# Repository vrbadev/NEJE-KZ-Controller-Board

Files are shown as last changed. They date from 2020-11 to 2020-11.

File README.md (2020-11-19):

# NEJE-KZ Controller Board
Reverse-engineered schematic and layout for NEJE-KZ laser engraver controller board.

The schematic should be the same as for the original board. Parts should be correctly identified and connected. My goal was to find out the wiring to be able to replace the damaged original board with a board with my own design.

**Warning:** The reconstructed layout has not been manufactured or tested. Weird things can be found on this allegedly $25-worth Chinese board.

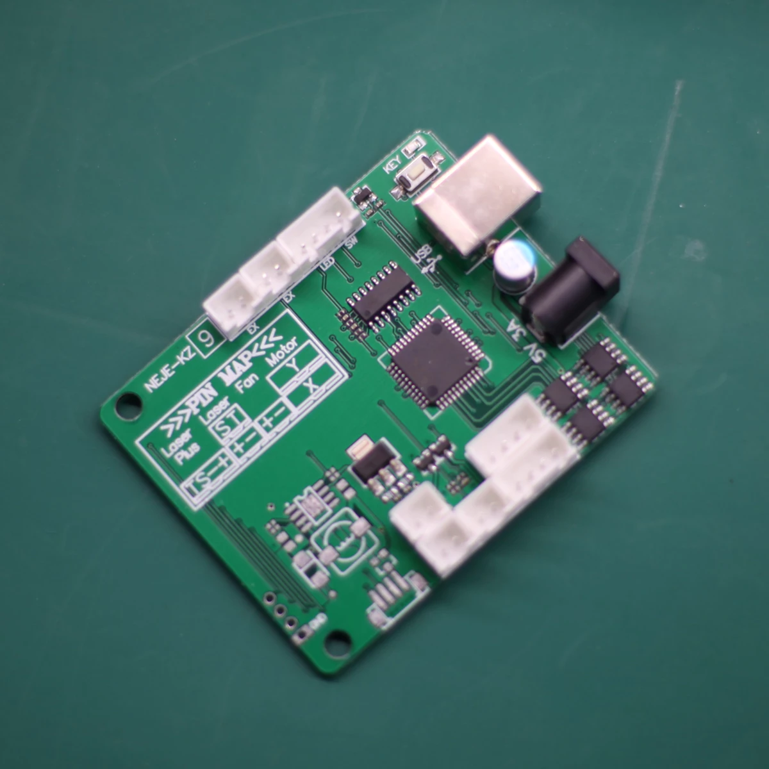
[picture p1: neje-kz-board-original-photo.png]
Original board photo
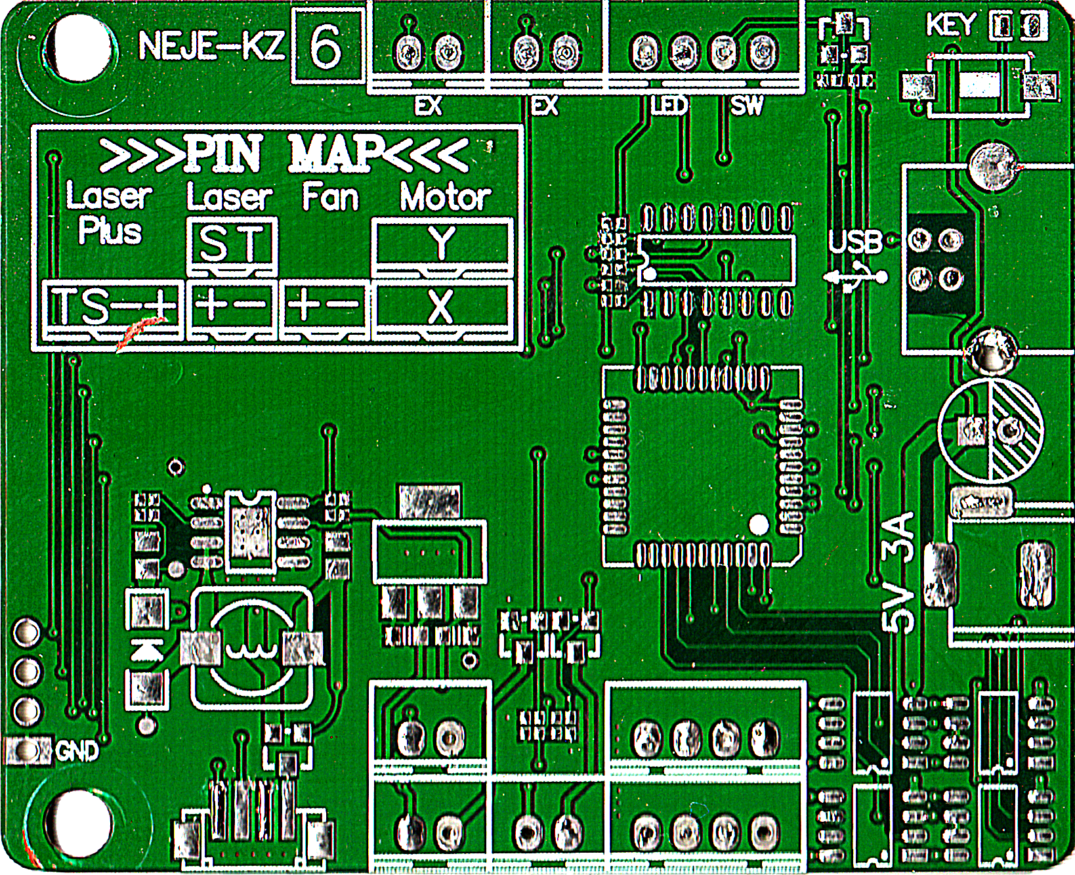
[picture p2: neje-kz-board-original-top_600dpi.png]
Original board - top scan
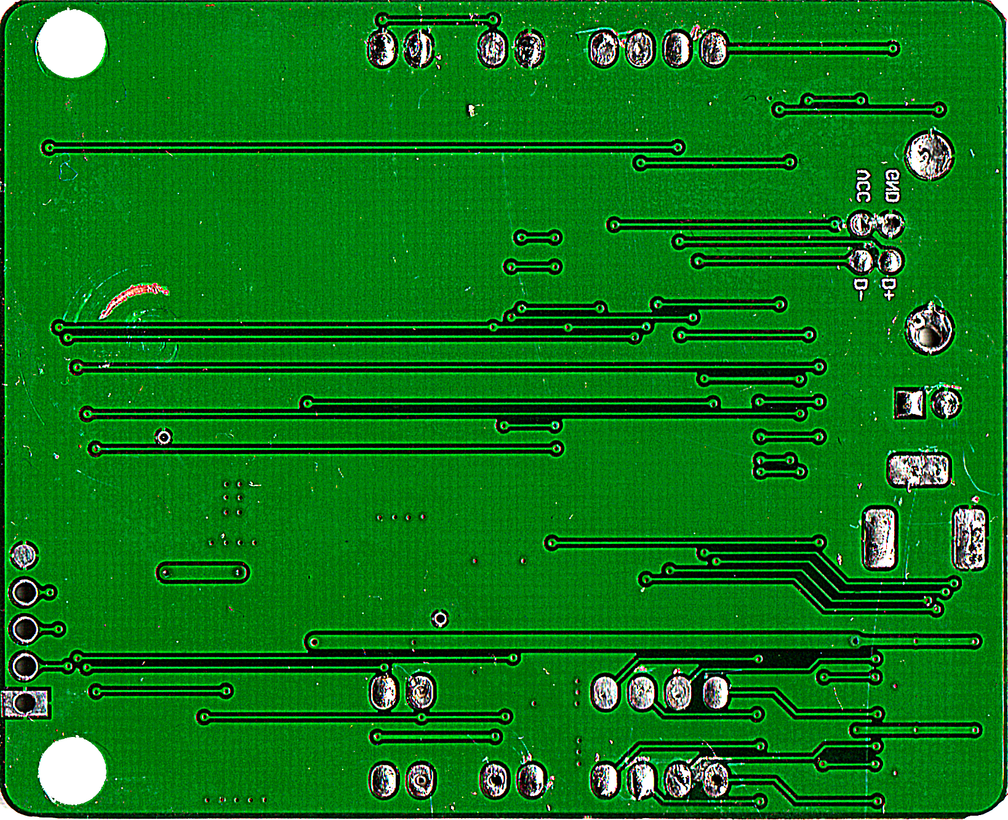
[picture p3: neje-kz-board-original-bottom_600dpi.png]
Original board - bottom scan
  

## BOM
| Qty | Part | Value | Package | Additional info |
|-----|---|---|---|---|
| 1 | C1 | 560u/6.3V | E2,5-7 | |
| 1 | C10 | 1n | 0402 | |
| 4 | C2, C4, C5, C8 | 100n | 0402 | |
| 1 | C3 | 2n7 | 0402 | |
| 2 | C6, C7 | 1u | 0603 | |
| 2 | C9, C11 | 1u | 0805 | |
| 1 | D1 | SS14 | SMA | Schottky diode, 40V, 1A |
| 1 | IC1 | STC8A4K16S2A12 | LQFP44-10X10 | STC8F family MCU |
| 1 | IC2 | XC6206P332MR | SOT23-3 | LDO, 3.3V, 200mA |
| 1 | IC3 | AMS1117-5.0 | SOT223 | LDO, 5.0V, 1A |
| 1 | IC4 | CH340C | SO16 | USB to Serial |
| 1 | IC5 | TX4223 | SOIC8 | DC-DC boost 5A converter |
| 4 | IC6, IC7, IC8, IC9 | TC118S | SOIC8 | Single channel DC motor driver |
| 1 | J1 | USB-B | USB-B-PTH | USB B THT connector |
| 1 | J10 | LASER-ST | JST-XH-02 | |
| 1 | J11 | LASER_PLUS | 1X04_1MM_RA  | |
| 1 | J12 | UART | MA04-1 | |
| 1 | J2 | DC 5.5/2.1mm | | THT DC jack connector |
| 2 | J3, J4 | EX | JST-XH-02 | |
| 1 | J5 | LED-SW | JST-XH-04 | |
| 1 | J6 | MOTOR-X | JST-XH-04 | |
| 1 | J7 | MOTOR-Y | JST-XH-04 | |
| 1 | J8 | FAN | JST-XH-02 | |
| 1 | J9 | LASER-PWR | JST-XH-02 | |
| 1 | L1 | 470UH | 8x8mm | Eg. WE 74477724 |
| 1 | LED1 | | 0805 | |
| 1 | Q1 | SI2301 | SOT23-3 | P-Channel MOSFET |
| 2 | Q2, Q3 | GMS2302AL | SOT23-3 | N-Channel MOSFET |
| 1 | R1 | 1k | 0402 | |
| 5 | R2, R3, R7, R8, R9 | 3k3 | 0402 | |
| 2 | R4, R10 | 10k | 0402 | |
| 1 | R5 | 270R | 0402 | |
| 1 | R6 | 6k2 | 0402 | |
| 1 | S1 | BTN | DTSM-3 | SMT Push-button |

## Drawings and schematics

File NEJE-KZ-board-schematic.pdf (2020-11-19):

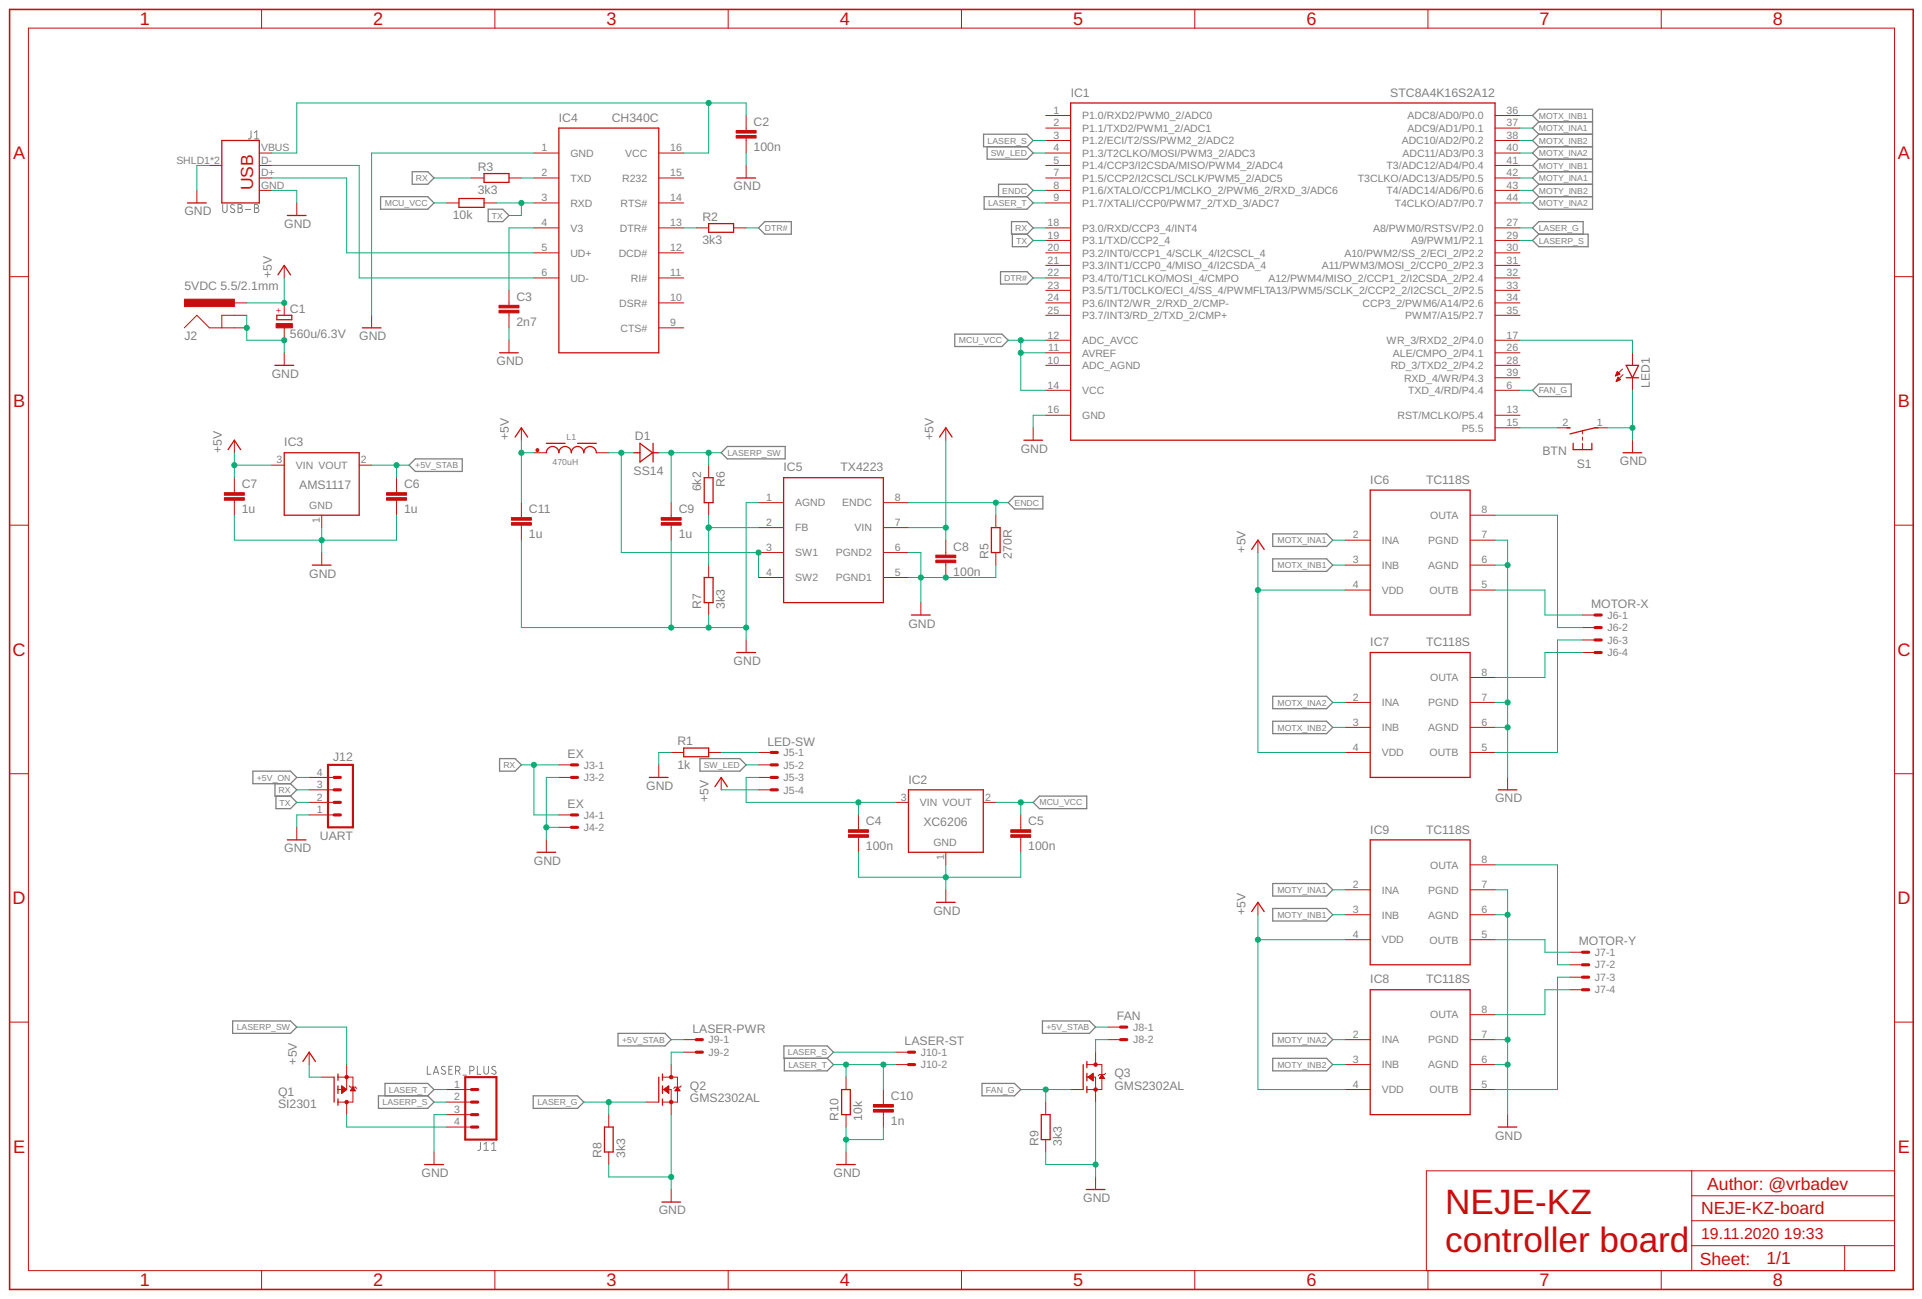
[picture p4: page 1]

TX | LASERP_S

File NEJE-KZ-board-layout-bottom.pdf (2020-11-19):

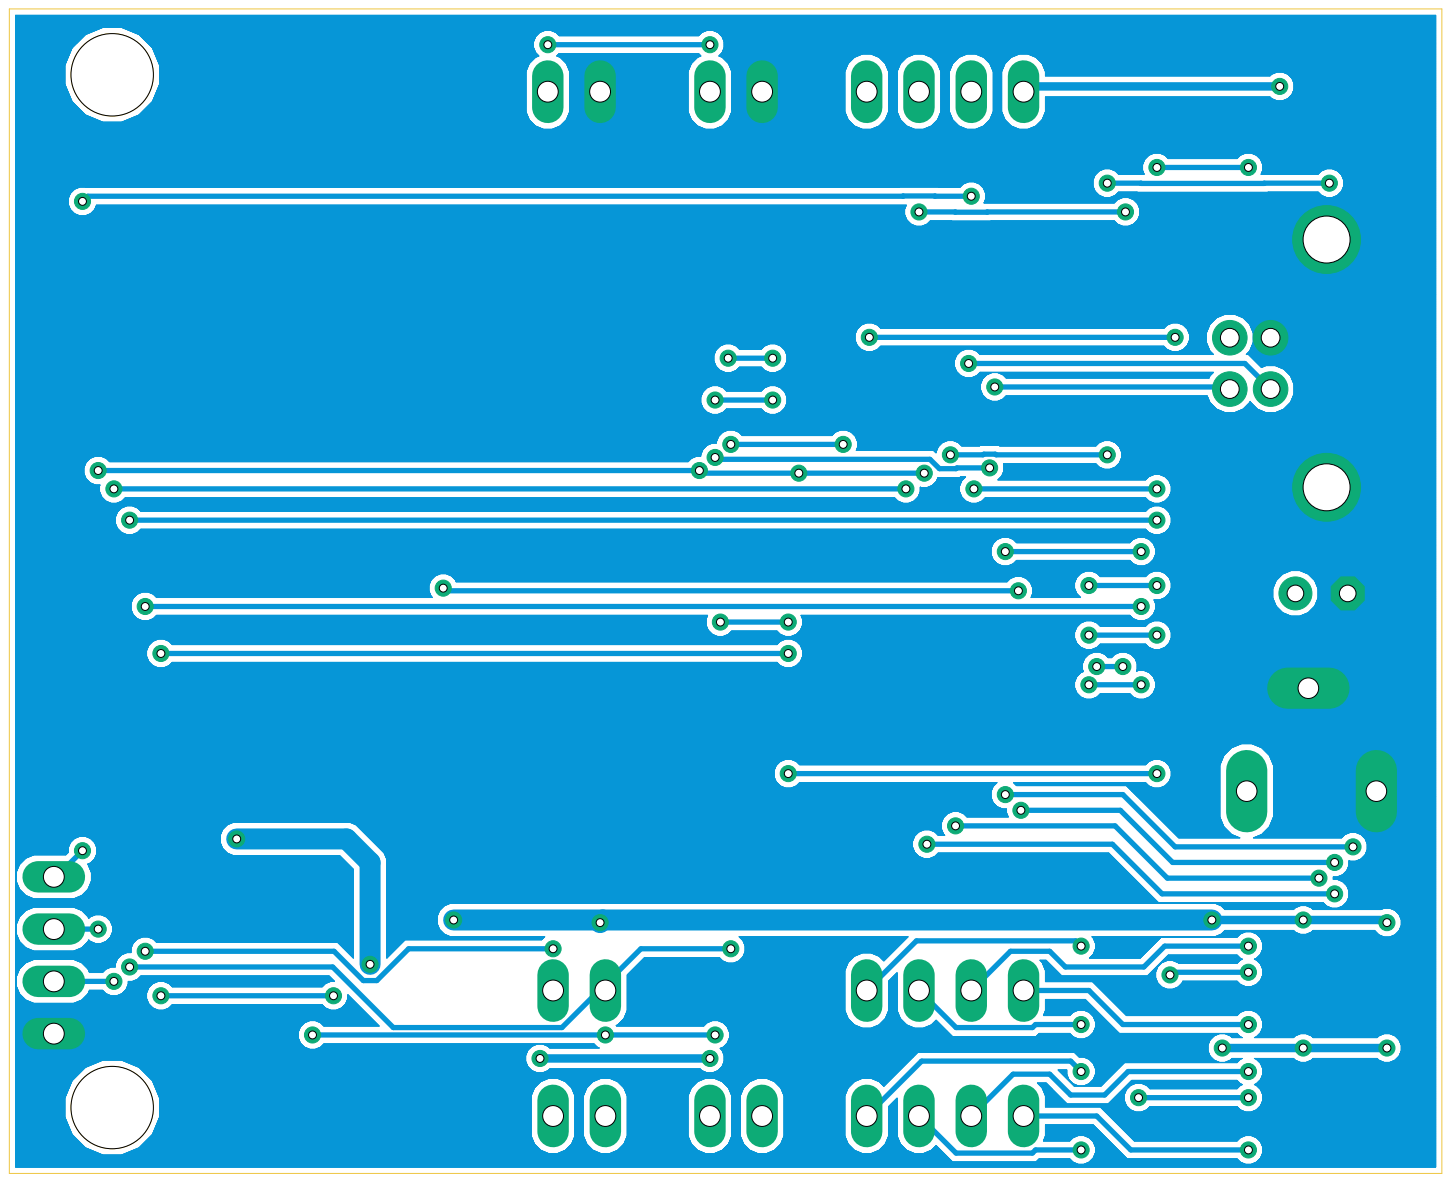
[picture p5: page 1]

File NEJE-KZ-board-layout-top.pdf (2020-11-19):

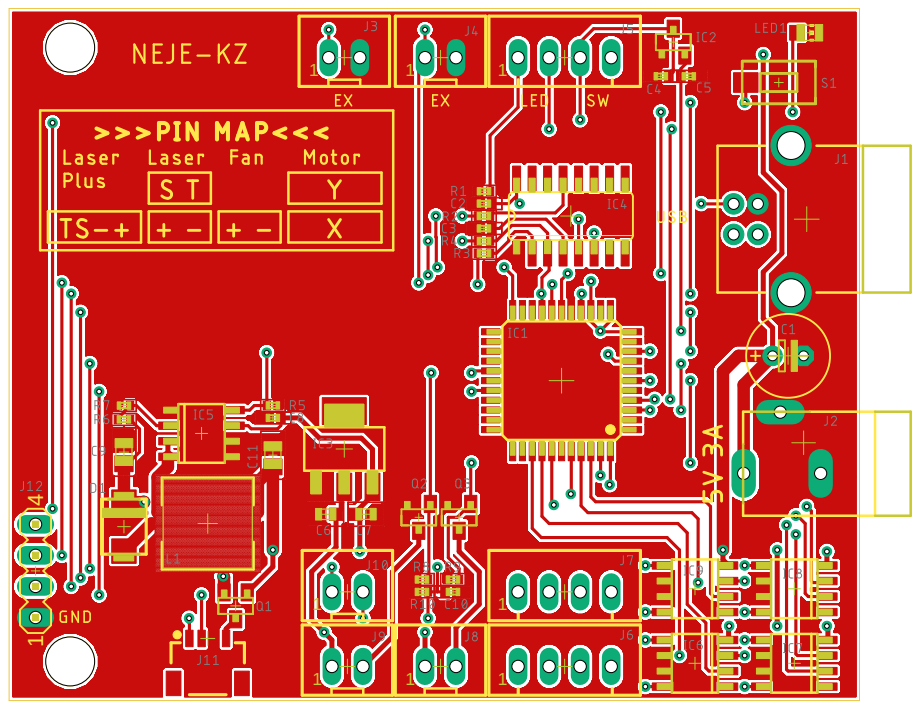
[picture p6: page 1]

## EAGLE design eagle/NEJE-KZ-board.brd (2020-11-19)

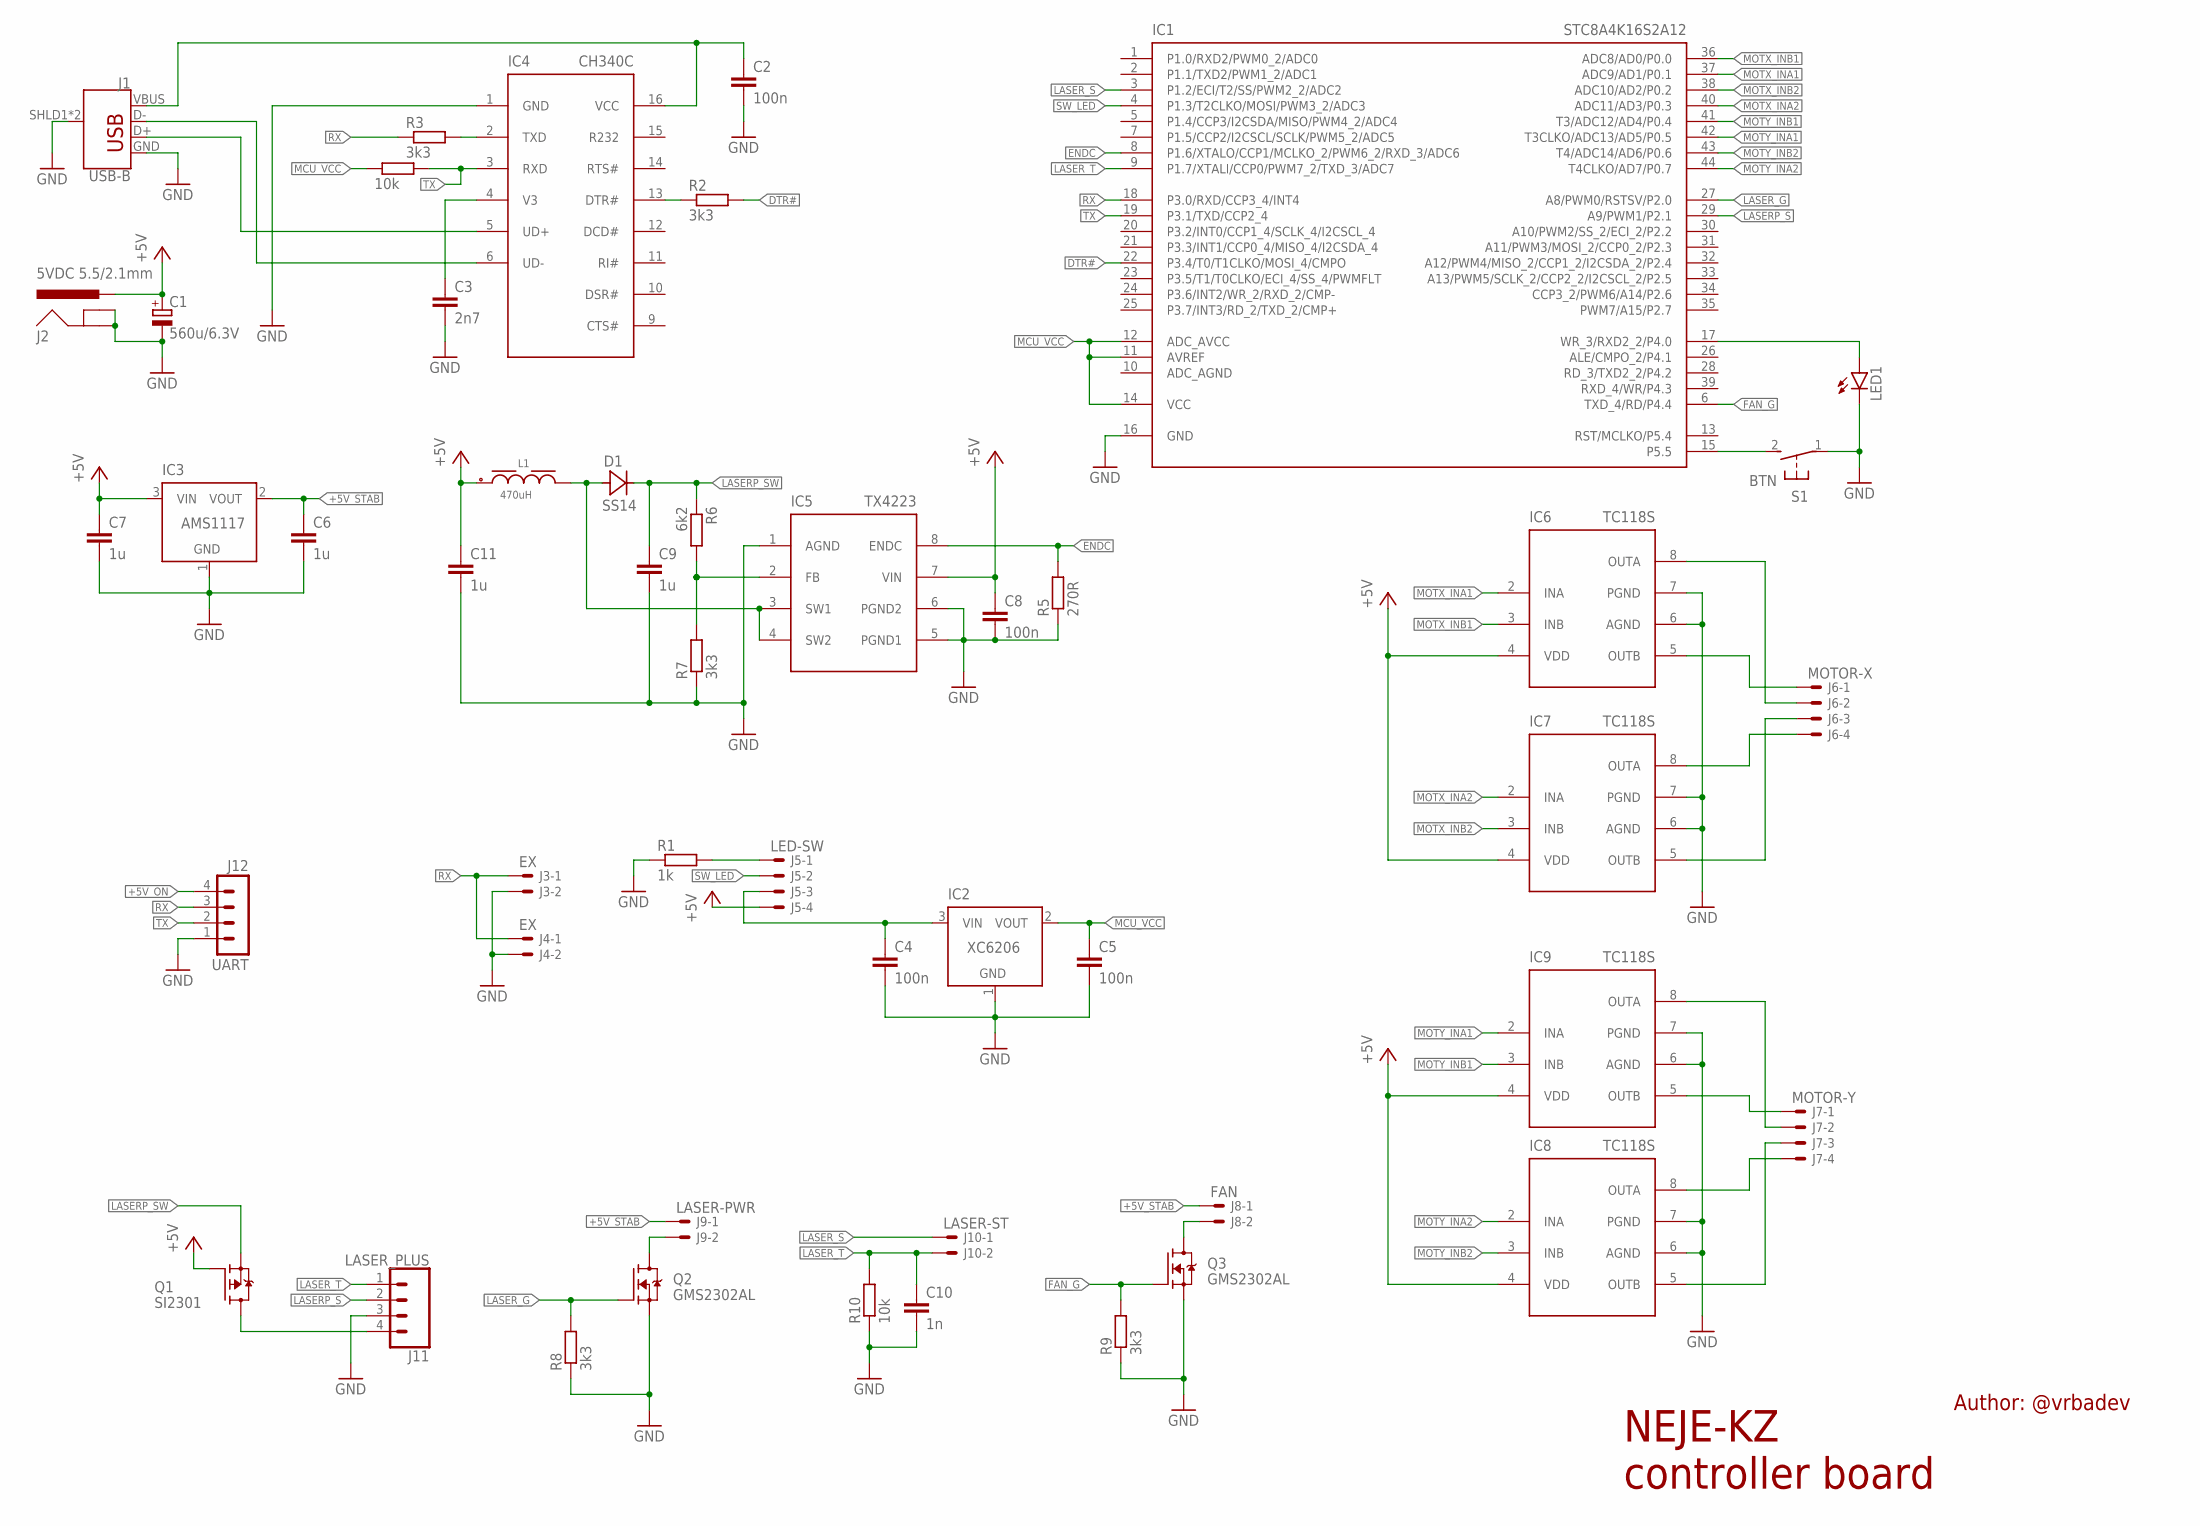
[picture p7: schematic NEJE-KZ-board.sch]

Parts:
C1: 560u/6.3V; E2,5-7
C2, C4, C5, C8: 100n; C0402
C3: 2n7; C0402
C6, C7: 1u; C0603
C9, C11: 1u; C0805
C10: 1n; C0402
D1: SS14; SMA
IC1: STC8A4K16S2A12; LQFP44-10X10
IC2: XC6206; SOT23-3
IC3: AMS1117; SOT223
IC4: CH340C; SO16
IC5: TX4223; SOIC8
IC6, IC7, IC8, IC9: TC118S; SOIC8
J1: USB-B; USB-B-PTH
J2: 5VDC 5.5/2.1mm; POWER_JACK_SLOT
J3, J4: EX; JST-XH-02-PACKAGE-LONG-PAD
J5: LED-SW; JST-XH-04-PACKAGE-LONG-PAD
J6: MOTOR-X; JST-XH-04-PACKAGE-LONG-PAD
J7: MOTOR-Y; JST-XH-04-PACKAGE-LONG-PAD
J8: FAN; JST-XH-02-PACKAGE-LONG-PAD
J9: LASER-PWR; JST-XH-02-PACKAGE-LONG-PAD
J10: LASER-ST; JST-XH-02-PACKAGE-LONG-PAD
J11: LASER_PLUS; 1X04_1MM_RA
J12: UART; MA04-1
L1: 470uH; WE-PD_7345
LED1: LEDCHIP-LED0805; CHIP-LED0805
Q1: SI2301; SOT23-3
Q2, Q3: GMS2302AL; SOT23-3
R1: 1k; R0402
R2, R3, R7, R8, R9: 3k3; R0402
R4, R10: 10k; R0402
R5: 270R; R0402
R6: 6k2; R0402
S1: BTN; DTSM-3

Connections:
+5V: C1.+, C7.1, C8.1, C11.1, IC3.3 (VIN), IC5.7 (VIN), IC6.4 (VDD), IC7.4 (VDD), IC8.4 (VDD), IC9.4 (VDD), J2.PWR, J5.4, L1.1, Q1.1 (G)
+5VUSB: C2.1, IC4.16 (VCC), J1.VBUS
+5V_ON: C4.1, IC2.3 (VIN), J5.3, J12.4
+5V_STAB: C6.1, IC3.2 (VOUT), J8.1, J9.1
BTN: IC1.15 (P5.5), S1.2
DTR#: IC1.22 (P3.4/T0/T1CLKO/MOSI_4/CMPO), R2.2
ENDC: IC1.8 (P1.6/XTALO/CCP1/MCLKO_2/PWM6_2/RXD_3/AD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), IC5.8 (ENDC), R5.2
FAN_G: IC1.6 (TXD_4/RD/P4.4), Q3.1 (G), R9.2
GND: C1.-, C2.2, C3.2, C4.2, C5.2, C6.2, C7.2, C8.2, C9.2, C10.2, C11.2, IC1.16 (GND), IC2.1 (GND), IC3.1 (GND), IC4.1 (GND), IC5.1 (AGND), IC5.5 (PGND1), IC5.6 (PGND2), IC6.6 (AGND), IC6.7 (PGND), IC7.6 (AGND), IC7.7 (PGND), IC8.6 (AGND), IC8.7 (PGND), IC9.6 (AGND), IC9.7 (PGND), J1.GND, J1.SHLD1 (SHIELD), J1.SHLD2 (SHIELD), J2.GND@1 (GNDBREAK), J2.GND@2 (GND), J3.2, J4.2, J11.3, J12.1, LED1.C, Q2.2 (S), Q3.2 (S), R1.1, R5.1, R7.1, R8.1, R9.1, R10.1, S1.1
LASERP_S: IC1.29 (A9/PWM1/P2.1), J11.2
LASERP_SW: C9.1, D1.C, Q1.2 (S), R6.1
LASER_G: IC1.27 (A8/PWM0/RSTSV/P2.0), Q2.1 (G), R8.2
LASER_S: IC1.3 (P1.2/ECI/T2/SS/PWM2_2/ADC2), J10.1
LASER_T: C10.1, IC1.9 (P1.7/XTALI/CCP0/PWM7_2/TXD_3/ADC7), J10.2, J11.1, R10.2
LED1: IC1.17 (WR_3/RXD2_2/P4.0), LED1.A
MCU_VCC: C5.1, IC1.11 (AVREF), IC1.12 (ADC_AVCC), IC1.14 (VCC), IC2.2 (VOUT), R4.1
MOTX_INA1: IC1.37 (ADC9/AD1/P0.1), IC6.2 (INA)
MOTX_INA2: IC1.40 (ADC11/AD3/P0.3), IC7.2 (INA)
MOTX_INB1: IC1.36 (ADC8/AD0/P0.0), IC6.3 (INB)
MOTX_INB2: IC1.38 (ADC10/AD2/P0.2), IC7.3 (INB)
MOTY_INA1: IC1.42 (T3CLKO/ADC13/AD5/P0.5), IC9.2 (INA)
MOTY_INA2: IC1.44 (T4CLKO/AD7/P0.7), IC8.2 (INA)
MOTY_INB1: IC1.41 (T3/ADC12/AD4/P0.4), IC9.3 (INB)
MOTY_INB2: IC1.43 (T4/ADC14/AD6/P0.6), IC8.3 (INB)
unnamed: C3.1, IC4.4 (V3)
unnamed: IC4.13 (DTR#), R2.1
unnamed: IC4.2 (TXD), R3.2
unnamed: J5.1, R1.2
unnamed: IC6.5 (OUTB), J6.1
unnamed: IC6.8 (OUTA), J6.2
unnamed: IC7.5 (OUTB), J6.3
unnamed: IC7.8 (OUTA), J6.4
unnamed: IC9.5 (OUTB), J7.1
unnamed: IC9.8 (OUTA), J7.2
unnamed: IC8.5 (OUTB), J7.3
unnamed: IC8.8 (OUTA), J7.4
unnamed: IC5.2 (FB), R6.2, R7.2
unnamed: J9.2, Q2.3 (D)
unnamed: J8.2, Q3.3 (D)
unnamed: J11.4, Q1.3 (D)
unnamed: D1.A, IC5.3 (SW1), IC5.4 (SW2), L1.2
RX: IC1.18 (P3.0/RXD/CCP3_4/INT4), J3.1, J4.1, J12.3, R3.1
SW_LED: IC1.4 (P1.3/T2CLKO/MOSI/PWM3_2/ADC3), J5.2
TX: IC1.19 (P3.1/TXD/CCP2_4), IC4.3 (RXD), J12.2, R4.2
USB_D+: IC4.5 (UD+), J1.D+
USB_D-: IC4.6 (UD-), J1.D-

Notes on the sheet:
NEJE-KZ controller board
Author: @vrbadev

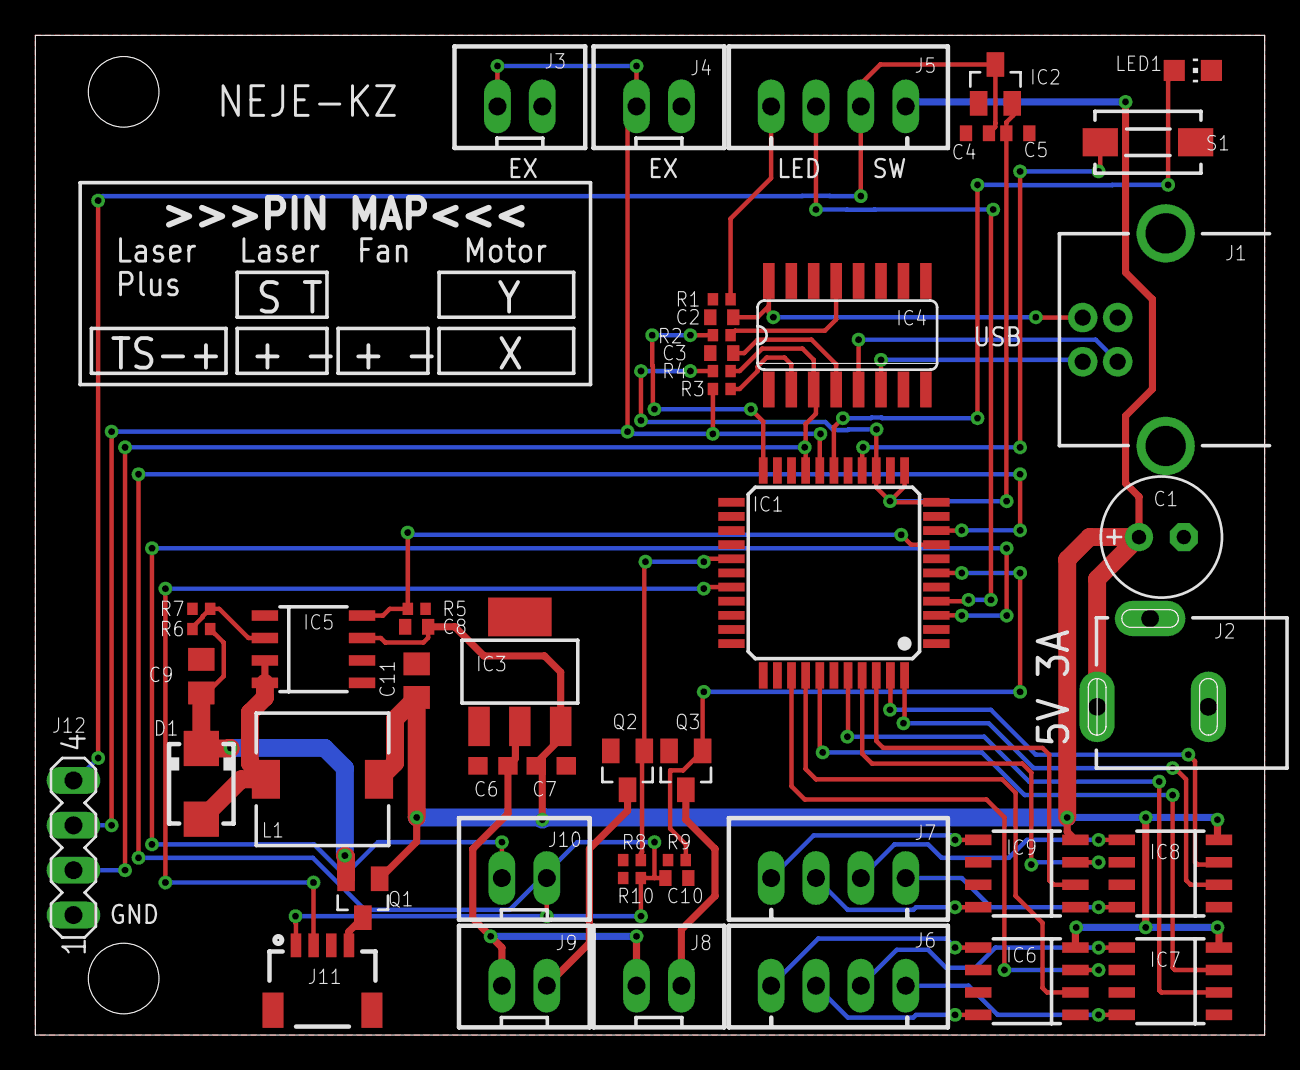
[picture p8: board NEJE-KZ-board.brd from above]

Board: 2 copper layers, 69.6 x 56.6 mm, 49 parts (0 on the bottom side), 46 nets.

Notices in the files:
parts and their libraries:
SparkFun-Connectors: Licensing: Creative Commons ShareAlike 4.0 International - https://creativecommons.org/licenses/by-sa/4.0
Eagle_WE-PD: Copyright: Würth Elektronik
